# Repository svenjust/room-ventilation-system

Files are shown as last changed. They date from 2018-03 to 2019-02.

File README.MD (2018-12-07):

# Steuerung einer Lüftungsanlage für Wohnhäuser

Diese Steuerung wurde als Ersatz der Originalsteuerung entwickelt.

Das Original war Pluggit P300. Diese Steuerung funktioniert ebenso für Pluggit P450 und viele
weitere Lüftungsanlagen.

Es werden:
1. zwei Lüfter angesteuert und deren Tachosignale ausgelesen
2. vier Temperatursensoren abgefragt
3. Steuerung Abluftventilator zum Frostschutz
4. Optional: Vorheizregister als Frostschutz 
5. Optional: Sommer-Bypass geschaltet
6. Optional: Bis zu zwei Temperatur- und Feuchtigkeitssensore auslesen
7. Optional: Luftqualitätsensor (VOC) und CO2 Sensor auslesen
Die Drehzahlregelung der Lüftermotoren erfolgt durch PID-Regler. Dies sorgt dafür, das die geforderten
Drehzahlen der Lüfter sicher erreicht werden. Die Leistungssteuerung des Vorheizregisters erfolgt
ebenfalls durch einen PID-Regler.

Differenzdrucksensoren werden bisher nicht berücksichtigt.

Die Steuerung ist per LAN (W5100) erreichbar. Als Protokoll wird mqtt verwendet. Über mqtt liefert
die Steuerung Temperaturen, Drehzahlen der Lüfter, Stellung der Bypassklappe, den Status der AntiFreeze
Funktion und sonstige Werte zurück und es können verschiedene Parameter gesetzt werden.

Zusätzlich bietet die Steuerung Unterstützung für TFT Touchscreen, um einerseits die Messwerte
anzuzeigen und andererseits die Steuerung zu konfigurieren. Touchkalibrierung erfolgt bei dem
ersten Touch oder nach langen Touch auf Hauptseite (8 Sekunden). Im Verzeichnis Screenshots
befinden sich ein paar [Screenshots](Screenshots/README.md).

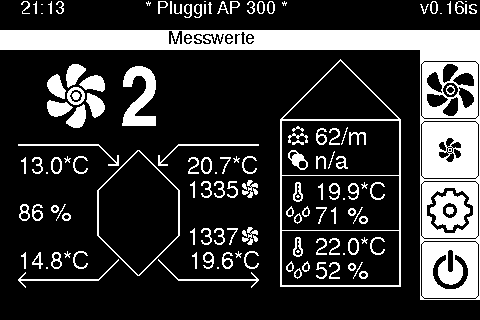
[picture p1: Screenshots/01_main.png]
Main screen


Im Verzeichnis Docs befindet sich weitere Dokumentation zu verschiedenen Themen.

Um das Projekt zu bauen müssen folgende Voraussetzungen erfüllt sein:
  - Folgende Libraries müssen installiert werden: SPI, EEPROM, PubSubClient,
    Adafruit_GFX_Library, DHT_sensor_library, PID, Adafruit_TouchScreen,
    DallasTemperature, Adafruit_Unified_Sensor, MCUFRIEND_kbv, OneWire,
    Wire, Ethernet
  - Das Projekt bringt eigene Libraries mit. Diese müssen ebenfalls installiert
    werden, am einfachsten als symbolische Links. Der Skript link_libs.sh
    linkt die Libraries an die (hoffentlich) richtige Stelle.

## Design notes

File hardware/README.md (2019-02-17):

Änderungen von HW-0.25 zu HW-0.26 - P300_Arduino_IF
 - Korrektur externer Displayanschluss zum Arduino

Änderungen von HW-0.23 zu HW-0.26 - P300_Display_IF
 - Korrektur Displayanschluss zum Display
 
Änderungen von HW-0.23 zu HW-0.25 - P300_Arduino_IF
 - Ergänzung von externen Pullup-Widerstand und Glättungskondensator am Tachosignal

Neu HW-0.25 - P300_Diff_Press
 - Entwurf einer Platine für den Aufbau von Differenzdrucksensoren
 
-----------------------------------------------------------------------------------------------------
12.01.2019 Version HW-0.24, nur P300_HiVolt, in die Platinenerstellung gegeben

Änderungen von HW-0.23 zu HW-0.24 - P300_HiVolt
 - Anschluss zu Relais per Schraubklemmen, anstatt Molex Stecker, wegen der schwierigen Beschaffung und Crimpen der Molex Verbindung
 - Alternative für 5V Spannung Meanwell IRM-05-5 mit 5W(1A) Leistung hinzugefügt, empfohlen bei Verwendung Display
 - Platine 3mm verlängert
 - Bohr in Mitte/unten hinzugefügt
 - Leiterbahnen zu den Lüftern auf 2mm verbreitert

 -----------------------------------------------------------------------------------------------------
09.01.2019 Version HW-0.23 in die Platinenerstellung gegeben

Änderungen von HW-0.22 zu HW-0.23 - P300_Arduino_IF
 - Linke Seite der Platine vergrößert auf ArduinoMega-Größe
 - Stecker für Displayanschluss ergänzt
 - Fünf weitere Bohrungen für Befestigung ergänzt
 - Leiterbahnen im größeren Abstand zu Durchbohrungen und Bauteilen verlegt
 - Connector für J12 I2C nach links verschoben, damit ausreichend Platz für JTS Stecker
 - Auf dem Stecker J4 sind die beiden Lüfteranschlüsse Lüfter 1 und Lüfter 2 getauscht. Damit ist der Stecker kompatibel zu Pluggit. Der Pluggit-Lüfter-Steuerstecker kann direkt aufgesteckt werden, wenn Molex Stiftleiste - KK - 1x8-polig - Stecker, Molex-Best-Nr. 22272081 verwendet wird.
 - Auf dem Stecker J4 (Lüfteranschluss) die vergessenen Masseverbindungen Pin 4 und Pin 8 ergänzt.

Änderungen von HW-0.22 zu HW-0.23 - P300_HiVolt
 - 230V Lüfteranschluss kompatibel zu Pluggit, Molex Stiftleiste - Mini-Fit Jr - 2x4-polig - Stecker, Molex-Best-Nr. 39281083
 - Stecker J3, J4 für Relais auf Molex Stiftleiste - Mini-Fit Jr - 2x3-polig - Stecker, Molex-Best-Nr. 39288060 geändert.
 - Änderung der Belegung der Stecker J3, J4 für die Verwendung es Relaisboards mit den Ralaisanschlüssen: Mitte = Stromzuführung, links = Nicht geschaltet, rechts geschaltet
 - Räumliche Trennung von 230V und Niedervoltspannungen auf der Platine
 - Bohrungen Pins Varistor auf 1mm vergrößert
 
Neu HW-0.23 - P300_Display_IF
 - Platine zum Aufstecken des Displays für die räumlich getrennte Montage von Display zu P300_Arduino_IF
 - Bohrlöcher für Befestigung hinzugefügt

Änderungen von HW-0.20 zu HW-0.21 - P300_Arduino_IF
 - Pins für Relais auf die ursprünglichen Pins zurückgelegt:
   D40 = BP_DIR, D41 = BP_POW, D42 = L2, D43 = L1
 - Pins für PWM-Signal Lüfter auf ursprüngliche Belegung zurückgelegt
   D44 = PWM_L1, D46 = PWM_L2

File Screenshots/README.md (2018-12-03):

Here a few screenshots from the controller UI:

Boot messages:

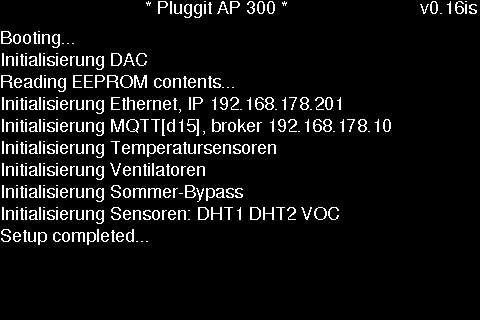
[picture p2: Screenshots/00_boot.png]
Boot


Main screen:

Main Screen
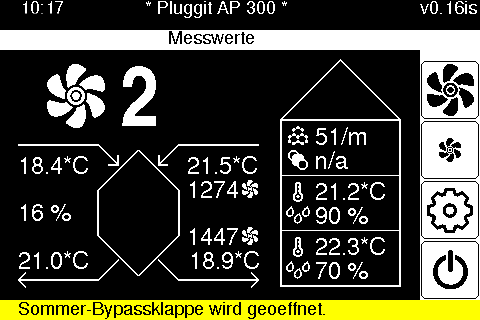
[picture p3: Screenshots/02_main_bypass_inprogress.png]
Opening Bypass

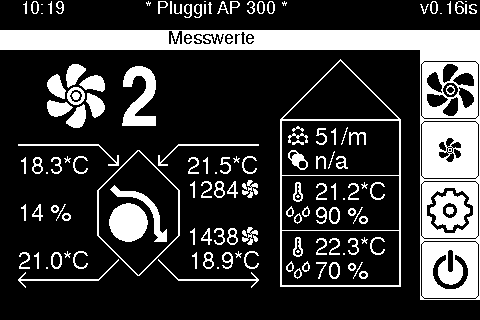
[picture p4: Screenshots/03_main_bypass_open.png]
Bypass Open

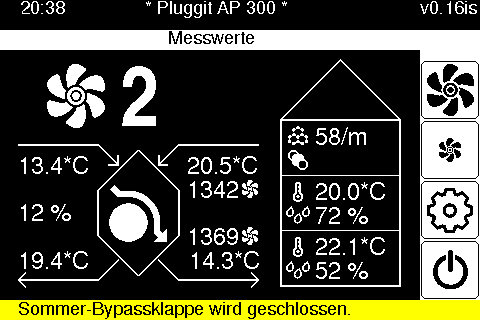
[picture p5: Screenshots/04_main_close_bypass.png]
Bypass Closing

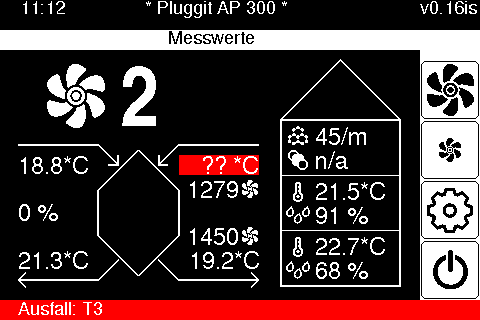
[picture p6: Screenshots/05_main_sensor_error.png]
Sensor Error


Calibration screen:

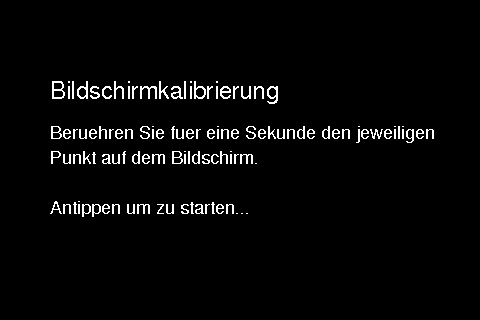
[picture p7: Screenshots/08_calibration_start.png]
Touchscreen Calibration

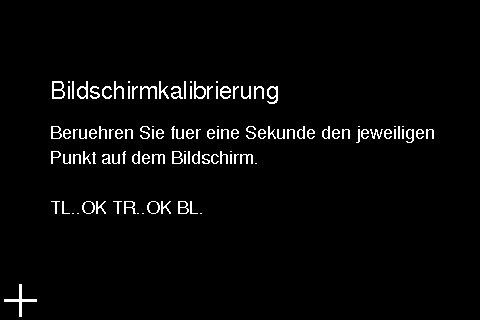
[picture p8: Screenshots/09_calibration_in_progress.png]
Touchscreen Calibration


Setup screen:

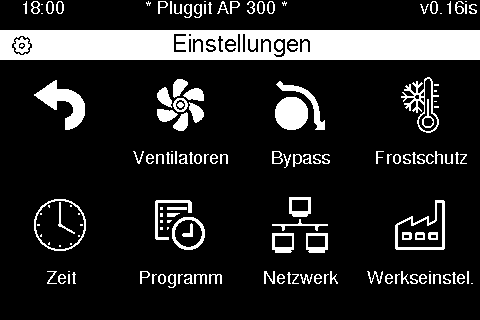
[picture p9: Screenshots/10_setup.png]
Setup


Fan setup screen:

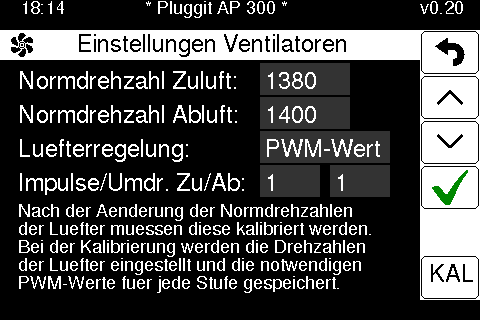
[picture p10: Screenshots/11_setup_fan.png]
Fan

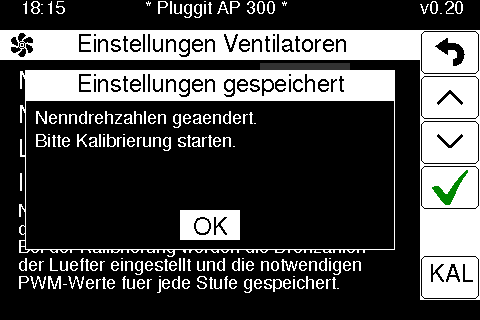
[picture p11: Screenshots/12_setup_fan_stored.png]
Fan Store

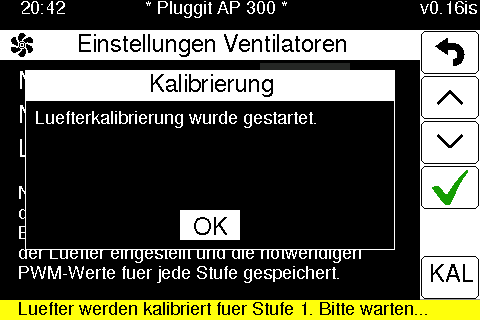
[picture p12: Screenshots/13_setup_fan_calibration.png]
Fan Calibration


Summer bypass setup screen:

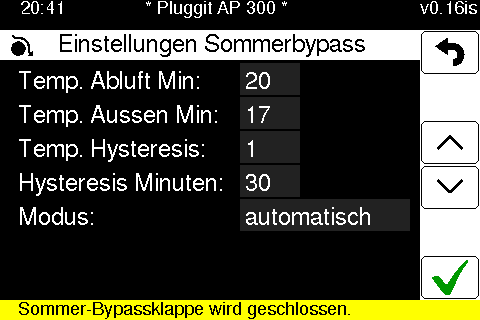
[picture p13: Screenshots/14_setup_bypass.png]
Bypass


Antifreeze setup screen:

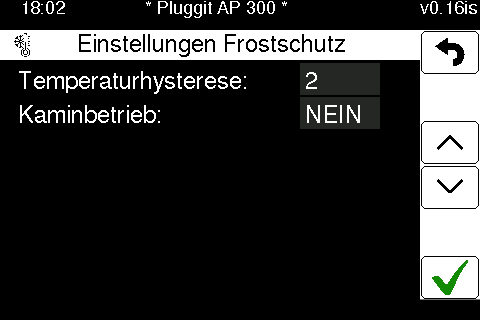
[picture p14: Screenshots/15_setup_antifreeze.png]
Antifreeze


Timezone and DST setup screen:

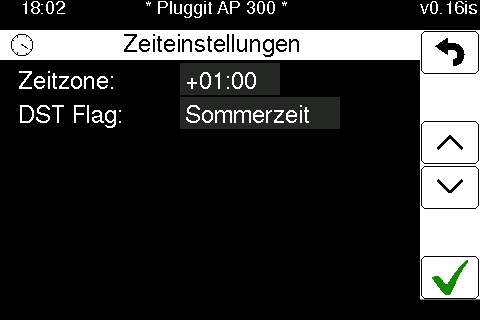
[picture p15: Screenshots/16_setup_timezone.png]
Time


Program manager screen:

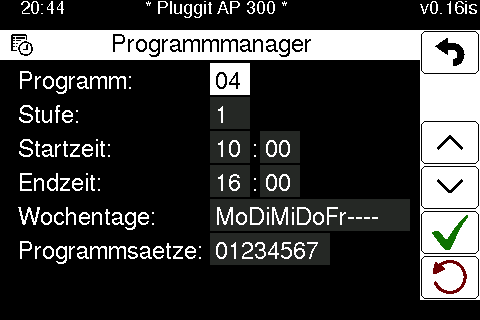
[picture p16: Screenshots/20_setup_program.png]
Program Manager

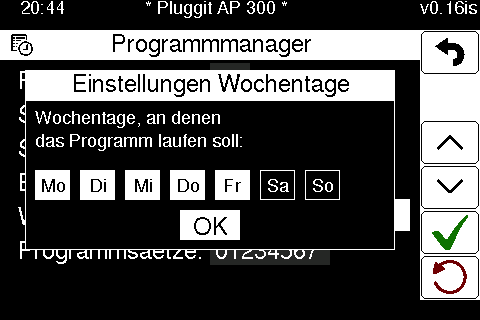
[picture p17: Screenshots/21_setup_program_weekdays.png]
Program Weekdays

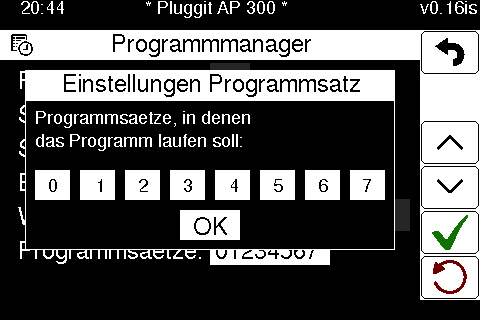
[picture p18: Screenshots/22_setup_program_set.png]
Program Sets


Network settings screen:

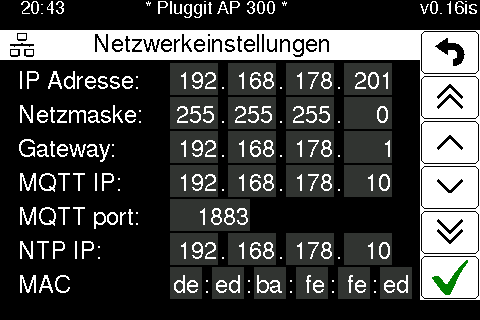
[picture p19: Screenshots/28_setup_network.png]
Network


Factory defaults screen:

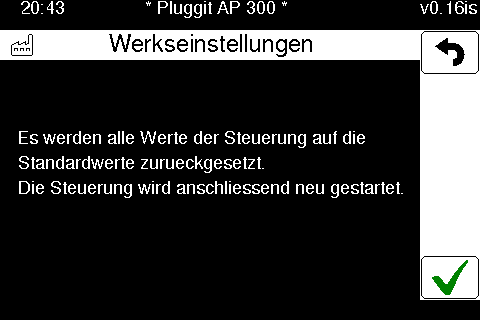
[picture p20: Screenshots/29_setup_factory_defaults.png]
Factory defaults


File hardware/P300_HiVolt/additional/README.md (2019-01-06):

# kicad
My KiCad libraries

HLK-PM02
HLK-PM03
HLK-PM12

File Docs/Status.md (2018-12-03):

# System Status Communication

The controller communicates system status via MQTT messages to a MQTT broker.
For this to work, at least the IP address and MQTT broker address have to be
configured in UserConfig.hpp (see KWLConfig::NetworkIPAddress and
KWLConfig::NetworkMQTTBroker). Network gateway address as well as DNS and NTP
server are derived from IP address by replacing the last octet with 1.

## Status MQTT Topics

Following status topics are defined:

Topic                                          | Value (Unit)      | Description
---------------------------------------------- | ----------------- | -------------------------------------------
`d15/state/kwl/heartbeat`                      | `online` / `offline` / HH:MM:SS | Online status of the system (see below).
`d15/state/kwl/statusbits`                     | `0xEEEEIIVV`      | Status bits indicating overall system state (see below).
`d15/state/kwl/fan1/speed`                     | #### (rpm)        | Speed of FAN1 (intake).
`d15/state/kwl/fan2/speed`                     | #### (rpm)        | Speed of FAN2 (exhaust).
`d15/state/kwl/aussenluft/temperatur`          | ###.## (ºC)       | Temperature of outside air.
`d15/state/kwl/zuluft/temperatur`              | ###.## (ºC)       | Temperature of inlet air.
`d15/state/kwl/abluft/temperatur`              | ###.## (ºC)       | Temperature of outlet air.
`d15/state/kwl/fortluft/temperatur`            | ###.## (ºC)       | Temperature of exhaust air.
`d15/state/kwl/effiencyKwl`                    | ## (%)            | Current efficiency.
`d15/state/kwl/lueftungsstufe`                 | typically 0-3     | Current ventilation mode.
`d15/state/kwl/dht1/temperatur`                | ###.## (ºC)       | Temperature reported by additional DHT1 sensor (if any).
`d15/state/kwl/dht2/temperatur`                | ### (%)           | Humidity reported by additional DHT1 sensor (if any).
`d15/state/kwl/dht1/humidity`                  | ###.## (ºC)       | Temperature reported by additional DHT2 sensor (if any).
`d15/state/kwl/dht2/humidity`                  | ### (%)           | Humidity reported by additional DHT2 sensor (if any).
`d15/state/kwl/abluft/co2`                     | #### (ppm)        | CO2 concentration measured by additional CO2 sensor (if any).
`d15/state/kwl/abluft/voc`                     | #### (ppm)        | Air pollutants concentration measured by additional VOC sensor (if any).
`d15/state/kwl/antifreeze`                     | `on` / `off`      | State of antifreeze protection.
`d15/state/kwl/summerbypass/flap`              | `open` / `closed` / `unknown` | State of summer bypass flap.
`d15/state/kwl/summerbypass/mode`              | `auto` / `manual` | Summer bypass mode.
`d15/state/kwl/summerbypass/TempAbluftMin`     | ### (ºC)          | Minimum outlet air temperature to consider for opening bypass flap.
`d15/state/kwl/summerbypass/TempAussenluftMin` | ### (ºC)          | Minimum outside air temperature to consider for opening bypass flap.
`d15/state/kwl/summerbypass/HystereseMinutes`  | ### (min)         | Hysteresis for bypass flap change in automatic mode.
`d15/state/kwl/summerbypass/HysteresisTemp`    | ## (ºC)           | Hysteresis temperature to open/close bypass flap.
`d15/state/kwl/heatingapp/combinedUse`         | `YES` / `NO`      | Indicates whether the ventilation system is used in conjuction with a fireplace.
`d15/state/kwl/program/index`                  | ##                | Currently running program index or -1 if none (see ProgramManager.md).
`d15/state/kwl/program/set`                    | #                 | Current program set (0-7, see ProgramManager.md).
`d15/state/kwl/program/`                       | (program string)  | Returned in response to program query (see ProgramManager.md).

NOTE: MQTT topics will be changed in the future to harmonize the language used
(with legacy topic compatibility).

## Heartbeat

The controller sends a heartbeat message once every 30s (by default, it can be configured
or turned off using KWLConfig::HeartbeatPeriod). This message either contains the word
`online` or time in format HH:MM:SS (if NTP is available and KWLConfig::HeartbeatTimestamp
is set to true).

If the connection to the broker breaks, a will message with value `offline` will
be left at the broker, so attached clients can react to the event.

## Status Bits

Status bits in form of a hexadecimal number `0xEEEEIIVV` indicate the overall status
of the system. Top 4 digits indicate error conditions, mid 2 digits indicate additional
information and lower 2 digits contain additional information value.

Error condition flags are OR-ed together to form an error status (`EEEE`):
    * 0001 - FAN1 (intake) not working
    * 0002 - FAN2 (exhaust) not working
    * 0004 - crash presence bit (see Programming/CrashDebugging.md)
    * 0008 - NTP time not yet synchronized or NTP server not answering
    * 0010 - T1 sensor (outside air) not working
    * 0020 - T2 sensor (inlet air) not working
    * 0040 - T3 sensor (outlet air) not working
    * 0080 - T4 sensor (exhaust air) not working

Info messages contain info type (`II`) and info value (`VV`). Following info types
are currently defined:
    * 00 - no additional information
    * 01 - calibration in progress, value indicates which mode is being calibrated
    * 02 - antifreeze is trying to raise temperature using preheater, value indicates
           preheater strength in %
    * 03 - antifreeze turned off one or both fans, value indicates 0 only intake,
           1 also exhaust, for fireplace mode
    * 04 - summer bypass is opening (value 1) or closing (value 0)

## Sensor Values

Sensor values for FAN1, FAN2 and temperature sensors are self-explanatory.

Sensor values for DHT1, DHT2, CO2 and VOC sensors will be only communicated, if
respective sensors are actually installed.

## Ventilation Mode

Current ventilation mode will be communicated upon change and periodically.

## Summer Bypass

Summer bypass state values are communicated when the state of the bypass changes and
periodically.

Summer bypass configuration is only communicated on-demand.

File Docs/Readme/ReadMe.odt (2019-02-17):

Ersatzsteuerung für eine Lüftungsanlage für Wohnhäuser
mit Touch-Display und
mqtt Anbindung


Abbildungsverzeichnis

Abbildung 1: Schaltplan Interface Sensoren – Arduino 10

Abbildung 2: Bestückte Interface Platine Sensoren Arduino mit Molexsteckverbindungen 11

Abbildung 3: HiVolt Schaltplan mit Schaltnetzteil(en) und Pluggit Lüfteranschluss 11

Abbildung 4: Bestückte HiVolt Platine 12

Abbildung 5: Schaltplan Display Platine 14

Abbildung 6: Display Platine zum Aufstecken des Displays 14

Abbildung 7: Kalibrieren des Touchdisplay 20

Abbildung 8: Kalibrierung Touch wird gestartet 20

Abbildung 9: Fehlerhafte Erkennung des Tachosignals (rpm) 23

Abbildung 10: Korrekte Erkennung des Tachosignals (rpm) 24

Abbildung 11: Arduino Mega 2560 REV Bild von Dsimic - Eigenes Werk, CC BY-SA 4.0, https://commons.wikimedia.org/w/index.php?curid=35850081 31

# Sicherheitshinweis

ACHTUNG 230V, LEBENSGEFAHR

EIGENES RISIKO BEIM NACHBAU

Die Lüfter, der Bypass und das Vorheizregister werden mit 230V Versorgungsspannung betrieben bzw. mit 230V Spannung (Bypass) gesteuert.

Für den Betrieb der Lüftungsanlage mit einer Feuerstätte ohne Fremdluftzufuhr, siehe Abschnitt 6.2

# Einführung

## Ziel

Ziel dieser Entwicklung ist es, defekte Steuerungen von Lüftungsanlagen für Wohnhäuser durch diese Eigenentwicklung zu ersetzen. Die Entwicklung des Projekt erfolgt in Freizeit als Hobby. Für die Entwicklung werden Standardbauteile verwendet. Dies sind: Arduino Mega, ein LAN-Modul, OneWire Temperatursensoren DS18B20, optional ist die Ansteuerung eines Vorheizregisters, die Ansteuerung für den Sommer-Bypass, Sensoren für CO2, VOC und Luftfeuchtigkeit sowie ein (Touch-) Grafikdisplay für die lokale Anzeige. Die Lüfter können per Optokoppler oder separaten DAC Digital Analog Converter (0-10V) angeschlossen werden. Diese Steuerung implementiert eine MQTT Schnittstelle für die Verbindung zur Haussteuerung.

Die Steuerung wurde ursprünglich für eine Pluggit P300 Anlage entwickelt, funktioniert ebenso für Pluggit P450 und viele weitere Lüftungsanlagen. Die elektrische Anpassung für unterschiedliche Lüftungsanlagen wird im Abschnitt Hardware beschrieben.

Die Steuerung implementiert die wesentlichen Funktionen zum technisch sicheren Betrieb der Lüftungsanlage. Die Frostschutzabschaltung des Zuluftventilators ist immer aktiv, eine Vereisung und damit ggfs Zerstörung des Wärmetauschers sollte damit ausgeschlossen sein. Voraussetzung ist der korrekte Anschluss der Temperatursensoren. Die Autoren dieser Software übernehmen KEINERLEI Garantie. Es werden die folgenden Sensoren/Aktoren geschaltet.

- zwei Lüfter werden angesteuert und deren Tachosignale werden ausgelesen
- vier Temperatursensoren werden abgefragt
- Steuerung des Zuluftventilator zum Frostschutz
- Steuerung des Abluft- und des Zuluftventilators zum Frostschutz bei Kaminbetrieb
- Optional: Vorheizregister als Frostschutz
- Optional: Sommer-Bypass geschaltet
- Optional: Bis zu 2 Temperatur/Luftfeuchtesensoren (DHT22)
- Optional: CO2-Sensor MH-Z14
- Optional: VOC-Sensor

Diese Steuerung stellt eine MQTT Schnittstelle zur Verfügung und kann darüber mit Automatisierungssystemen kommunizieren. Alle Topics der MQTT Schnittstelle sind in https://github.com/svenjust/room-ventilation-system/tree/master/Docs/mqtt%20topics dokumentiert.

Komfortfunktionen, wie die Regelung der Lüftungsanlage anhand eines VOC Sensors, sind nicht implementiert. Diese Regelungsaufgaben können in übergeordneten Haussteuerung besser, weil spezifischer für den eigenen Anwendungsfall, implementiert werden. Der Autor verwendet fhem für diese Aufgaben. Die Einbindung dieser Steuerung in fhem wird im Abschnitt 9 beschrieben. Die Messwerte der evtl. verbauten CO2, VOC, oder Feinstaubsensoren in der Lüftungsanlage werden per MQTT gepublishet.

## Systemaufbau

Die Steuerung der Lüftungsanlage kann autark betrieben werden.

Sinnvoll ist ein Betrieb mit einer übergeordneten Haussteuerung. Die Installation von fhem und eines MQTT Brokers werden vorausgesetzt und sind nicht Inhalt dieses Papiers.

## Regelungsstrategie der Steuerung

Der Inbetriebnehmer muss die Normdrehzahl für Zu- und Abluftventilator vorgeben. Differenzdrucksensoren sind nicht verbaut. Hersteller wie Helios verbauen auch keine solchen Sensoren. Pluggit stellt als Normdrehzahl jeweils 1.550 U/min werksseitig ein.

Die Steuerung versucht die vorgegebenen Drehzahlen für Zu- und Abluftventilator zu erreichen. Dem Lüfter wird als Stellgröße ein PWM-Signal oder eine Gleichspannung 0-10V vorgegeben. Über die Tacholeitung teilt der Lüfter über ein PWM Signal seine aktuelle Drehzahl mit. Im Normalbetrieb der Steuerung findet keine Regelung der Drehzahl statt. Die Steuerung kann in den Kalibrierungbetrieb gesetzt werden. Die Lüfter fahren dann die, für die verschiedenen Lüftungsstufen notwendigen Drehzahlen an, und ermitteln per PID-Regler das jeweils notwendige PWM-Signal. Das PWM-Signal für die Drehzahl für jede Lüftungsstufe wird dann getrennt für jeden Lüfter im EEPROM gespeichert. Im Normalbetrieb wird der Lüfter mit dem kalibrierten PWM Signal angesteuert. Die Strategie ist ähnlich dem Betrieb des Originalhersteller, hier findet zu definierten Zeiten (Montagsmorgens) eine „Kalibrierung“ statt. Die Kalibrierung muss per Touch-Display oder per MQTT gestartet werden.

## Speicherung des Anlagenparameter

Die für einen sicheren Betrieb erforderlichen Anlagenparameter werden im EEPROM des Arduino Mega gespeichert. Der Inhalt des EEPROMs kann im Sourcecode und per MQTT-Befehl gelöscht werden. Die Anlage wird damit auf die sogenannte „Werkseinstellungen“ zurückgesetzt. Die Werkseinstellungen definieren für die P300 einen sicheren Betriebszustand.

# Hardware

Der Hardwareaufbau kann in unterschiedlichen Ausbaustufen erfolgen, ebenso können verschiedene Sensoren ergänzt werden. Zuerst wird die absolut notwendige Hardware besprochen. Weiter unten folgen optionale Teile.

## Hardwareauswahl

### Notwendige Hardware

Für die Steuerung ist ein Arduino Mega erforderlich. Für die externe Kommunikation ist ein LAN-Shield erforderlich, aufgebaut und getestet ist das System mit WizNET (W5100) Ethernet Shield, siehe 11.2.

Die Temperaturen werden mit vier Temperatursensoren DS18B20 (siehe 11.5) im Edelstahlgehäuse erfasst und einzeln mit der Steuerung verkabelt. Durch die getrennte Verkabelung können die Sensoren sicher den Luftströmen zugeordnet werden. Für jeden Temperatursensor ist ein 4,7k Widerstand erforderlich.

In den KWL Geräten sind häufig Lüfter mit 230V Anschluss und Steuerung per 10V-PWM-Signal oder per Gleichspannung 0-10V verbaut. Den genauen Lüftertyp muss jeder für seine Anlage bestimmen. In den Pluggit Geräten P300/450 sind Lüfter von Papst verbaut, ähnlich wie http://img.ebmpapst.com/products/manuals/R3G190RC0503-BA-GER.pdf verbaut. In der gerade erwähnten Anleitung, Seite 9 sind die Schaltungsmöglichkeiten des Lüfters aufgeführt. Eine einfache Ansteuerung kann bei dem vorliegenden Lüfter durch Optokoppler erfolgen. Die Optokoppler werden direkt mit dem Lüfter verbunden, siehe Bild 1. Das Tachosignal kann direkt mit dem Arduino verbunden werden.

Hardwareliste (Mindestausstattung):

- 1 x Arduino Mega 2560
- 1 x LAN Module WizNET (W5100) Ethernet Shield
- 4 x OneWire DS18B20 in Edelstahlhülse

Die vollständige Bauteillisten sind im Abschnitt 10 aufgeführt.

#### Platine für Verbindung der Sensoren und Lüfter mit dem Arduino

Für die Verbindung des Arduino Mega mit den Lüftern, Temperatursensoren, Relaisboard und weiteren Sensoren ist in diesem Projekt ein Interface Board entwickelt worden. Der Stecker für die Lüftersteuerung kann direkt von der Pluggitplatine umgesteckt werden

Die technischen Unterlagen zu den Boards und die Gerberfiles für die Erstellung sind bei Github verfügbar https://github.com/svenjust/room-ventilation-system/tree/master/hardware.

#### Spannungsversorgung

Für die Spannungsversorgung gibt es zwei Alternativen. Zum einen ist eine Platine zum Anschluss der 230 V-Lüfter und Netzteil verfügbar. Zum anderen kann ein Standardnetzteil verwendet werden.

Auf der unten vorgestellten Platine für Spannungsversorgung können neben integrierten Step-Down-Netzteilen für 5V und 12V auch die 230V Stecker der Lüfter direkt von der Pluggitplatine umgesteckt werden. Die Platine enthält ist mit einer Littelfuse-Sicherung und einem Varistor als Überspannungsschutz aufgebaut.

### Alternative und optionale Hardware

#### Alternativ: DAC 0-10V für Vorheizregister und Lüfter

Alternativ zu den Optokopplern können die Lüfter mit einem 0-10V Gleichstromsignal angesteuert werden. Ein Arduino kann eine solche Gleichspannung nicht direkt zur Verfügung stellen. Ein Digital-Analog-Converter (DAC) wie z.B. https://www.horter-shop.de/de/home/93-bausatz-i2c-analog- (https://www.horter-shop.de/de/home/93-bausatz-i2c-analog-input-modul-5-kanal-10-bit-4260404260752.html)input-modul-5-kanal-10-bit-4260404260752.html (https://www.horter-shop.de/de/home/93-bausatz-i2c-analog-input-modul-5-kanal-10-bit-4260404260752.html) stellt die erforderliche Spannung bereit und kann einfach vom Arduino angesteuert werden.

Wenn ein Vorheizregister verwendet werden soll, ist die Ansteuerung per DAC evtl. notwendig.

#### Optional: TouchDisplay

Für eine Visualisierung am Gerät bzw. eine Bedienung ohne Automatisierungssystem kann ein Touchdisplay (siehe 11.6) verwendet werden. Die Steuerung setzt auf die mcufriend-Library auf und geht von einer Auflösung von 480x320 Pixel aus. Das Touchdisplay sollte wenigstens 3,5“ groß sein.

#### Optional: Platine für abgesetztes TouchDisplay

Das Display kann entweder direkt auf dem LAN Shield oder per Kabelverbindung entfernt von der Steuerung vor oder auf der Lüftungsanlage betrieben werden. Die direkte Verbindung mit dem LAN Shield kann beim Testen interessant sein. Für die entfernte Anbindung ist eine Platine verfügbar.

#### Optional: Sommer-Bypass per Relais

Wenn das Gerät einen Sommer-Bypass eingebaut hat, kann dieser ansteuert werden. Die Steuerung enthält die dafür notwendigen Funktionen.

GEFAHR: Verschiedene Gerätehersteller bauen bzgl der Ansteuerspannung unterschiedliche Lösungen ein. Hier ist vor Beginn genau zu prüfen, was im eigenen Gerät verbaut.

In Pluggit-Geräten der Serien P300/450 wird der Sommer-Bypass mit 230V~ geschaltet. Die Schaltung entspricht der klassischen Rolladensteuerung, d.h. für die Fahrdauer wird eine Spannung angelegt und nach Ausschalten der Spannung bleibt der Bypass in der aktuellen Stellung stehen.

Helios schaltet den Sommer-Bypass mit 24V=.

Die Schaltung für den Sommer-Bypass entspricht klassischen Rolladensteuerung, es werden zwei Relais verbaut, das erste Relais schaltet die Spannung, das zweite (Wechsel-) Relais bestimmt die Fahrrichtung.

#### Optional: CO2 Sensor

Mit dem folgenden CO2 Sensor hat der Autor gute Erfahrungen gemacht: MH-Z14, https://www.sensor-test.de//ausstellerbereich/upload/mnpdf/en/MHZ14_14.pdf . Das Signal wird über eine serielle Schnittstelle übertragen.

Die Messwerte des CO2 Sensors werden per MQTT an übergeordnete Geräte übertragen. Eine Regelung der Lüftungsanlage anhand des CO2-Sensors, ist nicht implementiert. Diese Regelungsaufgaben kann in einer übergeordneten Haussteuerung besser, weil spezifischer für den eigenen Anwendungsfall, implementiert werden.

Der CO2 Sensor kann im Abluftstrom der Lüftungsanlage verbaut werden.

#### Optional: VOC Sensor

Der Autor verwendet den folgenden VOC Sensor Figaro TGS2600, http://www.figarosensor.com/products/2600pdf.pdf . Das Signal wird durch einen Widerstandswert übertragen. Für das Steuern der Lüftungsanlage ist der VOC Sensor nach Erfahrung des Autors ausreichend, der CO2-Sensor dient eher dem Spiel- und Messtrieb. Beide Werte korrelieren weitgehend.

Die Messwerte des VOC Sensors werden per MQTT an übergeordnete Geräte übertragen. Eine Regelung der Lüftungsanlage anhand des VOC-Sensors, ist nicht implementiert. Diese Regelungsaufgaben kann in einer übergeordneten Haussteuerung besser, weil spezifischer für den eigenen Anwendungsfall, implementiert werden.

Der VOC Sensor kann im Abluftstrom der Lüftungsanlage verbaut werden.

#### Optional: Luftfeuchtesensoren DHT22

Für die Messung der Luftfeuchte im Abluft- und Zuluftstrom können bis zu zwei DHT22 Sensoren eingebaut werden. Die Messwerte der Sensoren werden per MQTT an übergeordnete Geräte übertragen. Eine Regelung der Lüftungsanlage anhand der DHT22-Sensoren, ist nicht implementiert.

## Schaltpläne

### Interface Platine für Anschluss der Sensoren

Abbildung 1: Schaltplan Interface Sensoren – Arduino

Für die Verbindung zu den Lüftern wird ein achtpoliger Molex-Stecker mit der Bezeichnung:Molex_KK-254_AE-6410-08A_1x08_P2.54mm_Vertical empfohlen. Damit kann der Stecker der Pluggit-Platine direkt umgesteckt werden, das Pinlayout ist identisch.

Für die anderen 2-, 3-, 4-, 6- und 8-poligen Steckverbindern können Stecker mit 2,54mm Pinabstand verwendet werden. Dies können Steckverbinder aus der Molex-KK-254-Reihe oder auch JST XH-Reihe sein. Die JST XH-Reihe ist aktuell leichter und zu geringeren Kosten verfügbar.

Abbildung 2: Bestückte Interface Platine Sensoren Arduino mit Molexsteckverbindungen

### HiVolt Platine für Stromversorgung und 230V Anschluss der Lüfter

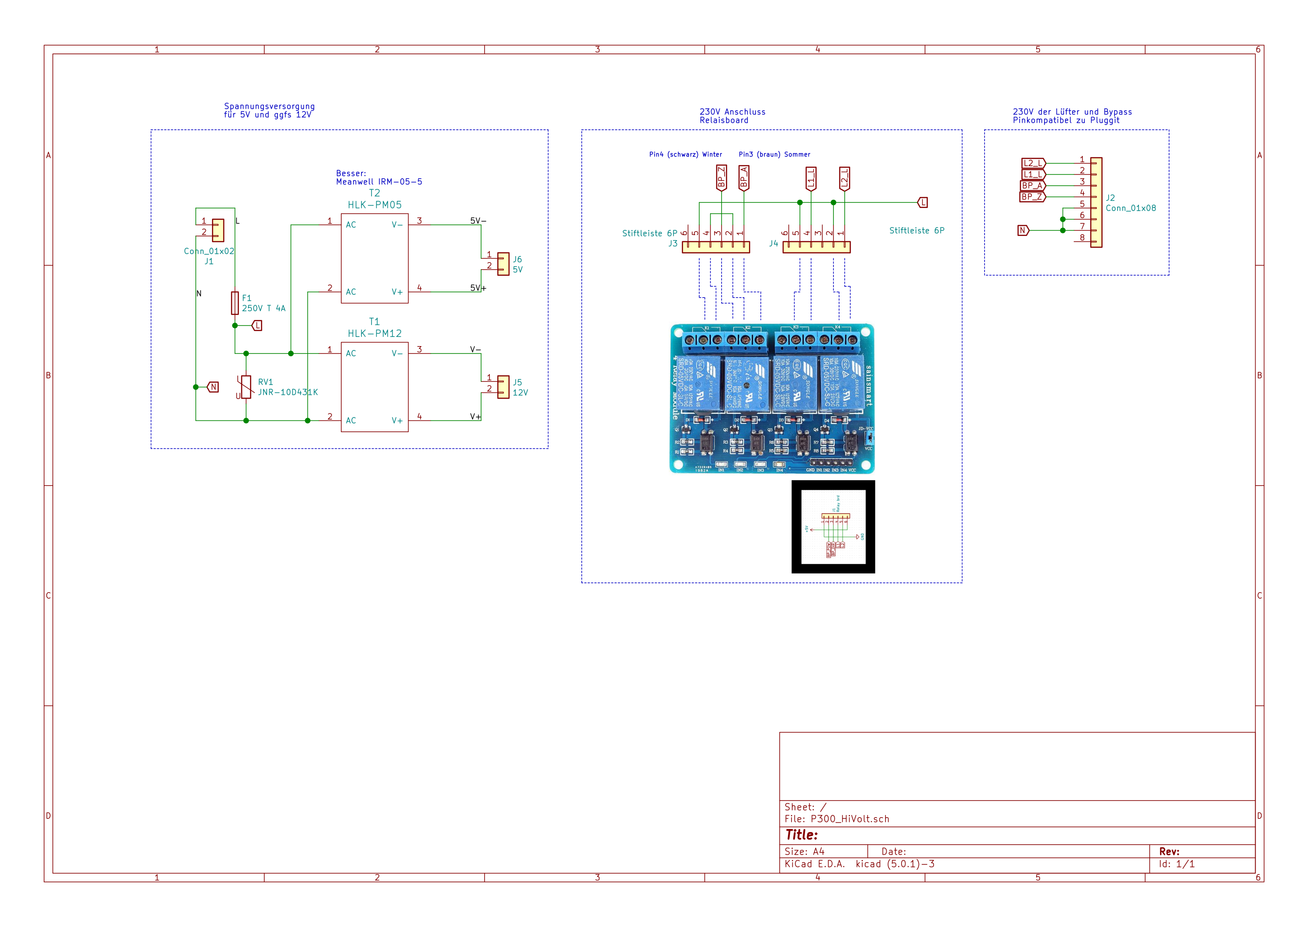
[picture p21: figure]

Abbildung 3: HiVolt Schaltplan mit Schaltnetzteil(en) und Pluggit Lüfteranschluss

Für das 5V Schaltnetzteil wird ein Meanwell IRM-05-5 empfohlen, dieses leistet bis zu 1A. Das HLK-PM5 kann beim Betrieb ohne Display verwendet werden. Die 12V Spannungsversorgung ist optional.

Für die 230V Verbindung zu den Lüftern wird der Connector Molex_Mini-Fit_Jr_5566-08A_2x04_P4.20mm_Vertical verwendet, dieser ist pinkompatible zu den Pluggit-Steckern, der Stecker kann umgesteckt werden.

Für den 230V Eingangsstecker wird Molex_Mini-Fit_Jr_5566-02A_2x01_P4.20mm_Vertical empfohlen, wiederum pinkompatible zu Pluggit.

Abbildung 4: Bestückte HiVolt Platine

### Interface Platine für Display

Abbildung 5: Schaltplan Display Platine

Abbildung 6: Display Platine zum Aufstecken des Displays

Die Interface Platine zum Display ermöglicht lediglich die einfache Befestigung und Verwendung von Steckern zwischen Display und Controller. Die Platine enthält keine weiteren Bauelemente.

## Aufbau der Platinen

Es wird ein fachkundigen Aufbau der Schaltung vorausgesetzt. Dabei ist zwischen der Niederspannungsseite und der 230V-Seite zu trennen.

Für den Aufbau der Schaltung existieren fertige Platinen. Die Verbindungen der Bauteile sind zu löten, bzw. zu schrauben. Nach dem Löten sind die Lötverbindungen zu kontrollieren.

Der Arduino Mega, die Interface Platine und das LAN Shield werden in der Reihenfolge von unten nach oben aufeinander gesteckt. Bei einer Verschraubung der Platinen sind Kunststoffschrauben zu verwenden.

Für die Befestigung der Platinen in der Lüftungsanlage kann als Träger eine zugeschnittene PVC Platte (Bastelplatte) verwendet werden. Um die Festigkeit zu erhöhen können links und rechts schmale Verstärkungen hochkant aufgeklebt werden. Die PVC Platte sorgt gleichzeitig für eine elektrische Trennung, insbesondere der HiVolt-Platine, gegenüber dem Gehäuse der Lüftungsanlage. Bei vollständiger Bestückung der HiVolt-Platine können die 230V führenden Leiterbahnen damit nicht mehr direkt berührt werden.

### Bestückung der Interface Platine

Die Bestückung der Interface Platine sollte mit den Optokopplern starten. Anschließend die Stecker der Kabelverbinder und die Verbinder zum Arduino einlöten. Für die korrekte Ausrichtung der Verbinder zum Arduino ist es sinnvoll, die Stiftleisten in den Arduino Mega zu stecken und anschließend erst die Platine auf die Stiftleisten zu stecken. Die Stiftleisten dann auf der Platine verlöten. Für die Stiftleisten zum LAN-Modul den Platine vom Arduino entfernen und die Stiftleisten mit dem LAN-Modul verbinden, die Platine auflegen und von unten verlöten. Nachfolgend die stehenden Widerstände und ggf. Kondensatoren einlöten.

Zu Abschluss der Bestückung auf Fehler (Lötbrücken, kalte Lötstelle) kontrollieren.

### Bestückung der HiVolt Platine

Die Bestückung der HiVolt Platine sollte mit der Fassung für die Sicherung und dem Varistor starten. Nachfolgend die Verbinder und Schaltnetzteile einlöten.

Zu Abschluss der Bestückung auf Fehler (Lötbrücken, kalte Lötstelle) kontrollieren.

### Bestückung der Interface Platine zum Display

Auf der Interface Platine müssen die Stiftleisten zum Display verlötet werden. Der Anschluss der Leitungen zur Interface Platine zum Arduino kann abhängig von der gewünschten Bauhöhe unterschiedlich ausgeführt werden, hier ist lediglich auf die korrekte Polung zu achten, Pin 1 ist bei beiden Verbindern gekennzeichnet.

Zu Abschluss der Bestückung auf Fehler (Lötbrücken, kalte Lötstelle) kontrollieren.

# Grundeinstellungen Soucecode

Die benutzerdefinierten Einstellungen sollen in der Datei UserConfig.h erfolgen. Diese Einstellungen bleiben auch bei einem Update des Sourcecodes erhalten. Die Syntax in der UserConfig.h lautet:

CONFIGURE(name, value)
CONFIGURE(name, values…)

Weitere Hinweise siehe in der Datei KWLConfig.h

## Definition der Anschlüsse

Abhängig vom tatsächlichen Aufbau der Hardware müssen die Anschlüsse (PINs) für Ein- und Ausgänge kontrolliert bzw. umdefiniert werden, insbesondere werden Displays unterschiedlich angeschlossen. Aktuell verwenden wir Displays für die Anschlüsse A0-A9 und 0-13.

Für die Auswertung des Tachosignals der Lüfter sind Interrupt-fähige Eingänge notwendig, aktuell Pin 18, 19. Das PWM Signal für die Lüfter wird an Pin 44 und Pin 46 bereitgestellt.

Der DAC verwendet die Anschlüsse 20 und 21.

Der CO2-Sensor MH-Z14 verwendet die zweite seriellen Schnittstelle Serial2, Pin 16 und 17.

Die Temperatursensoren DS18B20 verwendet die Pins 30 bis 33.

Die Luftfeuchtesensoren DHT1 und DHT2 verwenden die Pins 28 und 29.

Das Relais für den Bypass und die Lüfter verwendet die Anschlüsse 40 bis 43.

Der VOC Sensor verwendet den Analogeingang A15.

Im Sourcecode beginnt und endet der konfigurierbare Bereich mit „A N S C H L U S S E I N S T E L L U N G E N“

## Netzwerkeinstellungen

Es muss die MAC- und die IP Adresse, Subnet, Gateway, DNS dieser Steuerung einstellt werden, ebenso die IP-Adresse des mqtt-Brokers.

CONFIGURE(NetworkIPAddress, 192, 168, 20, 201)
CONFIGURE(NetworkGateway, 192, 168, 20, 250)
CONFIGURE(NetworkDNSServer, 192, 168, 20, 250)
CONFIGURE(NetworkNTPServer, 192, 168, 20, 250)
CONFIGURE(NetworkMACAddress, 0x02, 0xC8, 0x07, 0xC2, 0x35, 0x81 )

## Werkseinstellung

Die für einen Betrieb erforderlichen Anlagenparameter werden im EEPROM des Arduino Mega gespeichert.

Durch das Setzen von #define FACTORY_RESET_EEPROM true wird bei jedem Neustart der Steuerung der EEPROM-Speicher des Arduinos gelöscht und mit den Werkseinstellungen überschrieben. Für den regulären Betrieb muss #define FACTORY_RESET_EEPROM false definiert sein. Das EEPROM des Arduinos ist für 100.000 Schreibzyklen ausgelegt.

Alternativ kann das EEPROM mit dem

mosquitto_pub -t d15/set/kwl/resetAll_IKNOWWHATIMDOING -m YES

gelöscht werden. Anschließend wird die Steuerung neu gestartet.

Es sind die folgenden „Werkseinstellungen“ definiert. Die können in der Datei „UserConfig.h“ überschrieben werden.

Name | Wert | Beschreibung
StandardModeCnt | 4 | Anzahl der unterschiedlichen Lüftungsstufen
StandardKwlModeFactor | {0, 0.7, 1, 1.3} | Definition der Drehzahl je Stufe in Relation zu defStandardSpeedSetpointFan
StandardKwlMode | 2 | Standardlüftungsstufe beim Einschalten.
StandardSpeedSetpointFan1 | 1550 | Drehzahl in Standardlüftungsstufe für den Zuluftventilator
StandardSpeedSetpointFan2 | 1550 | Drehzahl in Standardlüftungsstufe für den Abluftventilator
StandardFan1ImpulsesPerRotation | 1.0 | Anzahl der Impulse am Tachosignal pro Umdrehung des Lüfters
StandardFan2ImpulsesPerRotation | 1.0 | Anzahl der Impulse am Tachosignal pro Umdrehung des Lüfters
StandardKwlFanPrecisionPercent | 1.5 | Max Abweichung der Istdrehzahl zur Solldrehzahl bei Kalibrierung in Prozent
StandardNenndrehzahlFan | 3200 | Nenndrehzahl des verbauten Ventilators, siehe Typenschild. Die Nenndrehzahl wird benötigt für die Berechnung der Ansteuerung im unkalibrierten Betrieb
StandardBypassTempAbluftMin | 24 | Mindestablufttemperatur für die Öffnung des Bypasses im Automatik Betrieb
StandardBypassTempAussenluftMin | 13 | Mindestaussenlufttemperatur für die Öffnung des Bypasses im Automatik Betrieb
StandardBypassHystereseMinutes | 60 | Hysteresezeit für eine Umstellung des Bypasses im Automatik Betrieb
StandardBypassHysteresisTemp | 3 | Hysteresetemperatur für eine Umstellung des Bypasses im Automatik Betrieb
StandardBypassManualSetpoint | 1 (Closed) | Stellung der Bypassklappen im manuellen Betrieb
StandardBypassMode | 0 (Auto) | Automatik oder manueller Betrieb der Bypassklappe. Im Automatikbetrieb steuert diese Steuerung die Bypass-Klappe, im manuellen Betrieb wird die Bypass-Klappe durch mqtt-Kommandos gesteuert.
StandardAntifreezeHystereseTemp | 3 | Hysteretemperatur für Steuerung von Antifreeze
StandardHeatingAppCombUse | false | Einstellung für den Feuerstättenbetrieb. false = keine Feuerstätte, true = Feuerstätte, Kamin, Ofen ohne Fremdluftzufuhr
StandardDST | false | Daylight savings time default settings.
StandardTimezoneMin | 60 | Standard time zone offset in minutes (CET, GMT+1).

## Ansteuerung der Relais

Für die Lüfter und den Sommer-Bypass können bis zu vier Relais verbaut sein. Ohne Sommer-Bypass kann die Steuerung auch ohne Relais betrieben werden. Da verschiedene Relais unterschiedlich geschaltet werden, kann hier die logische Schaltung definiert werden.

RELAY_ON | LOW | Daylight savings time default settings.
RELAY_OFF | HIGH | Standard time zone offset in minutes (CET, GMT+1).

## Debugausgaben

### Debugausgaben auf der seriellen Schnittstelle

Es können Debugausgaben auf der seriellen Schnittstelle für unterschiedliche Bereiche ein oder ausgeschaltet werden. Nach Änderung muss der Sourcecode neu kompiliert werden.

// *************************************************** D E B U G E I N S T E L L U N G E N ********************************************************

// Allgemeine Debugausgaben auf der seriellen Schnittstelle aktiviert.

static constexpr bool serialDebug = false;

// Debugausgaben für die Lüfter auf der seriellen Schnittstelle aktiviert.

static constexpr bool serialDebugFan = false;

// Debugausgaben für die Antifreezeschaltung auf der seriellen Schnittstelle aktiviert.

static constexpr bool serialDebugAntifreeze = false;

// Debugausgaben für die Summerbypassschaltung auf der seriellen Schnittstelle aktiviert.

static constexpr bool serialDebugSummerbypass = false;

// Debugausgaben für die Displayanzeige.

static constexpr bool serialDebugDisplay = false;

// Debugausgaben für die Sensoren.

static constexpr bool serialDebugSensor = false;

// Debugausgaben für das Programm.

static constexpr bool serialDebugProgram = false;

// *******************************************E N D E *** D E B U G E I N S T E L L U N G E N *****************************************************

### Debugausgaben per mqtt

Es können Debugausgabe per mqtt ein- und ausgeschaltet, sowie per mqtt übertragen werden. Dazu ist in der UserConfig.h

#define DEBUG

zu definieren. Anschließend können die Debugausgaben zur Laufzeit per mqtt ein- und ausgeschaltet werden. Die mqtt Topics sind in der Datei https://github.com/svenjust/room-ventilation-system/Docs/mqtt topics/mqtt_topics.ods beschrieben.

# Build der Software für Arduino

Die Software wird in der Arduino IDE gebaut. Debugausgaben für die serielle Schnittstelle können im Code aktiviert werden, siehe 4.5.1

## Notwendige Bibliotheken

Für das Bauen der Steuerung sind Bibliotheken notwendig.

- SPI,
- EEPROM,
- PubSubClient,
- Adafruit_GFX_Library,
- DHT_sensor_library,
- PID,
- Adafruit_TouchScreen,
- DallasTemperature,
- Adafruit_Unified_Sensor,
- MCUFRIEND_kbv,
- OneWire,
- Wire,
- Ethernet

Das Projekt bringt eigene Libraries mit. Diese müssen ebenfalls installiert werden, am einfachsten als symbolische Links. Der Skript link_libs.sh linkt die Libraries an die (hoffentlich) richtige Stelle.

Aktuelle Infos sind zu finden unter: https://github.com/svenjust/room-ventilation-system

# Inbetriebnahme

Vor der Inbetriebnahme sind unbedingt die Pinbelegungen für die Motoren und Sensoren, die Netzwerkeinstellungen und die „Werkseinstellungen“ zu kontrollieren und entsprechend den eigenen Bedürfnissen einzustellen. WICHTIG: Wenn Werkseinstellungen im Sourcecode geändert werden, muss das EEPROM gelöscht werden, damit die neuen Werkeinstellungen verwendet werden, siehe 4.3.

Eine schrittweise Inbetriebnahme wird empfohlen. Die Inbetriebnahme kann über das Touchdisplay oder den MQTT Broker erfolgen, diese Anleitung geht vom funktionierenden MQTT Broker aus.

## Displaykalibrierung

Für die Inbetriebnahme und auch für den späteren Betrieb der Anlage ist ein Display hilfreich. Der Touch vom Display muss nach dem Zusammenbau bzw. bei Änderung der Verbindung zwischen Display und Controller neu kalibriert werden. Dazu 10 Sekunden den Touch berühren, die Display-Kalibrierung wird gestartet.


Abbildung 8: Kalibrieren des Touchdisplay

Anschließend den Anweisung auf dem Display folgen.


Abbildung 9: Kalibrierung Touch wird gestartet

## Feuerstättenmodus (Kaminbetrieb)

Wenn eine Feuerstätte (Kamin/Ofen) im Haus ohne Fremdluftzufuhr betrieben wird, besteht die Gefahr, dass bei negativen Außentemperaturen der Zuluftlüfter abgeschaltet wird und giftiges Kohlenmonoxid (CO) aus der Feuerstätte in das Haus gesaugt werden.

- LEBENSGEFAHR -

Mit dem Einstellen des Feuerstättenmodus werden im Antifrostbetrieb beide Lüfter für vier Stunden ausgeschaltet. Das Wiedereinschalten vor vier Stunden ist nur durch einen Neustart der Steuerung möglich.

Der Feuerstättenmodus kann auf zwei Arten eingeschaltet werden, entweder im Sourcecode oder durch Zusenden einer MQTT Nachricht. Bei beiden Arten wird die Einstellung im EEPROM gespeichert und bleibt bei einem Neustart erhalten. Empfohlen wird die Einstellung im Sourcecode anzupassen, da diese Einstellung auch bei einer Rücksetzung auf Werkeinstellungen erhalten bleibt.

In der UserConfig muss eingestellt werden:

CONFIGURE(StandardHeatingAppCombUse, true)

Anschließend ist eine Rückstellung auf Werkseinstellungen notwendig, siehe 4.3.

Alternativ kann folgendes per MQTT an die Steuerung geschickt werden:

mosquitto_pub -t d15/set/kwl/heatingapp/combinedUse -m YES

Diese Einstellung wird gespeichert, aber bei einer Werkeinstellungen zurückgesetzt!

Beim Starten der Steuerung kann die Einstellung überprüft werden, es wird beim Feuerstättenmodus ausgegeben:

...System mit Feuerstaettenbetrieb

## Optional, aber empfohlen: MQTT Broker

Für den Betrieb ist ein MQTT Broker sinnvoll. Die Installation eines MQTT Brokers ist an vielen Stellen im Netz beschrieben, u.a. hier: https://wiki.fhem.de/wiki/MQTT_Einf%C3%Bchrung (https://wiki.fhem.de/wiki/MQTT_Einführung). Wenn der MQTT-Broker installiert ist und die Steuerung gestartet wird, so sendet die Steuerung alle 30 Sekunden ein Heartbeat Signal, diese kann bei einem Mqtt-Client mit

mosquitto_sub -v -h localhost -t d15/state/kwl/heartbeat

abonniert werden.

## Temperatursensoren

Die vier Temperatursensoren (DS18B20) sind notwendig für einen sicheren Betrieb der Lüftungsanlage. Bei niedrigen Außentemperaturen kann ansonsten der Wärmetauscher durch Frost zerstört werden.

Die Temperatursensoren sind an die Platine anschließen. Im Sourcecode ist die Variable serialDebug = 1 setzten und auf den Arduino flashen. Im seriellen Monitor werden die Temperaturen bei Änderung angezeigt. Für eine Temperaturänderungen können die Sensoren in die Hand genommen werden. Temperaturen von -127.0 zeigen, dass der Sensor nicht gefunden wurde.

Wenn die Temperatursensoren in der Anlage verbaut und verkabelt sind, sollte die korrekte Zuordnung zu den Luftströmen überprüft werden. Bei einer Außentemperatur von 5°C und einer Wohnraumtemperatur von 22 °C hat die Außenluft (T1) die geringste Temperatur, etwa 8 °C, anhängig von den baulichen Gegebenheiten. Die Zuluft (T2) wird bei etwa 18°C liegen. Die Abluft (T3) wird bei etwa 21°C und die Fortluft (T4) bei etwa 10°C liegen (T1 < T4 < T2 < T3). Wird diese Reihenfolge nicht eingehalten, es entweder die Außentemperatur sehr hoch oder die Zuordnung der Temperatursensoren zu den Luftströmen ist nicht korrekt.

## Lüfter

Da die Lüfter üblicherweise mit Netzspannung betrieben werden, ist besondere Vorsicht und Fachkenntnis notwendig.

Die Lüfter sind mit Netzspannung versorgen und an die Platine anschließen. Im Sourcecode die Variable serialDebugFan = 1 setzten und in der UserConfig.h #define DEBUG definieren, kompilieren und den Arduino flashen. Im seriellen Monitor werden die Drehzahlen bei Änderung angezeigt. Hier sollte überprüft werden, dass das Tachosignal der Lüfter korrekt erkannt wird (siehe auch 6.5.1).

Für den erfolgreichen Betrieb der Lüftungsanlage ist die korrekte Drehzahlerkennung die Voraussetzung.

### Überprüfung des Tachosignals vom Lüfters

Bei der Inbetriebnahme hat sich die korrekte Erkennung des Tachosignals als nicht immer einfach herausgestellt. Die Firma Pluggit hat während der Bauzeit der Anlage AP300 unterschiedliche Lüfter verbaut. Die Tachosignale der Lüfter haben sich als „unterschiedlich“ gut herausgestellt. Ob die Erkennung korrekt funktioniert, kann mit dem Python-Tool plotfans.py grafisch überprüft werden.

https://github.com/svenjust/room-ventilation-system/Docs/debug_fans/plotfans.py

Hinweise siehe: https://github.com/svenjust/room-ventilation-system/issues/11

Das Skipt plotfans.py stellt die Werte der Soll-, Istdrehzahl und PWM Signal der Lüfter grafisch dar. Das Script benötigt die „mqtt-Logausgabe“ der Lüfter. Um eine Logausgabe für die Lüfter mit Soll-, Istdrehzahl und PWM Signal zu bekommen ist das folgende Vorgehen erforderlich:

Die Software für den Arduino muss mit #define DEBUG kompiliert werden. Die Übertragung muss für jeden Lüfter muss einzeln aktiviert werden.

mosquitto_pub -t d15/debugset/kwl/fan1/getvalues -m on
mosquitto_pub -t d15/debugset/kwl/fan2/getvalues -m on

Die übertragenen Werte können mit der folgenden Zeile in einer Datei "/tmp/debug.log" protokolliert werden:

mosquitto_sub -v -h localhost -t "d15/debugstate/#" > /tmp/debug.log

Die Werte aus der Datei "/tmp/debug.log" können durch das Script plotfans.py dargestellt werden. Im Verzeichnis /tmp werden zwei Dateien mit der grafischen Darstellung der Drehzahlen von Lüfter 1 und 2 angelegt.

python <Pfad zu Script>\plotfans.py --infile /tmp/debug.log --out /tmp

Der folgende Aufruf zeigt die weiter möglichen Aufrufparameter:

python <Pfad zu Script>\plotfans.py -h zeigt die Aufrufparameter

Das folgende Bild zeigt im oberen Diagramm einen Lüfter mit fehlerhafter Tachosignalerkennung, die Schwankungen der Drehzahl (rpm: Revolution per minute) sind viel zu groß (600 bis etwa 1100 U/min bei gleichem PWM-Signal (ssf).

Im unteren Diagramm wird die Differenz zwischen der Solldrehzahl und der erkannten Istdrehzahl (GAP) dargestellt. Auch hier erkennt man die starken Schwankungen von 500 U/min (+/-250) bei gleichbleibenden PWM-Signal.

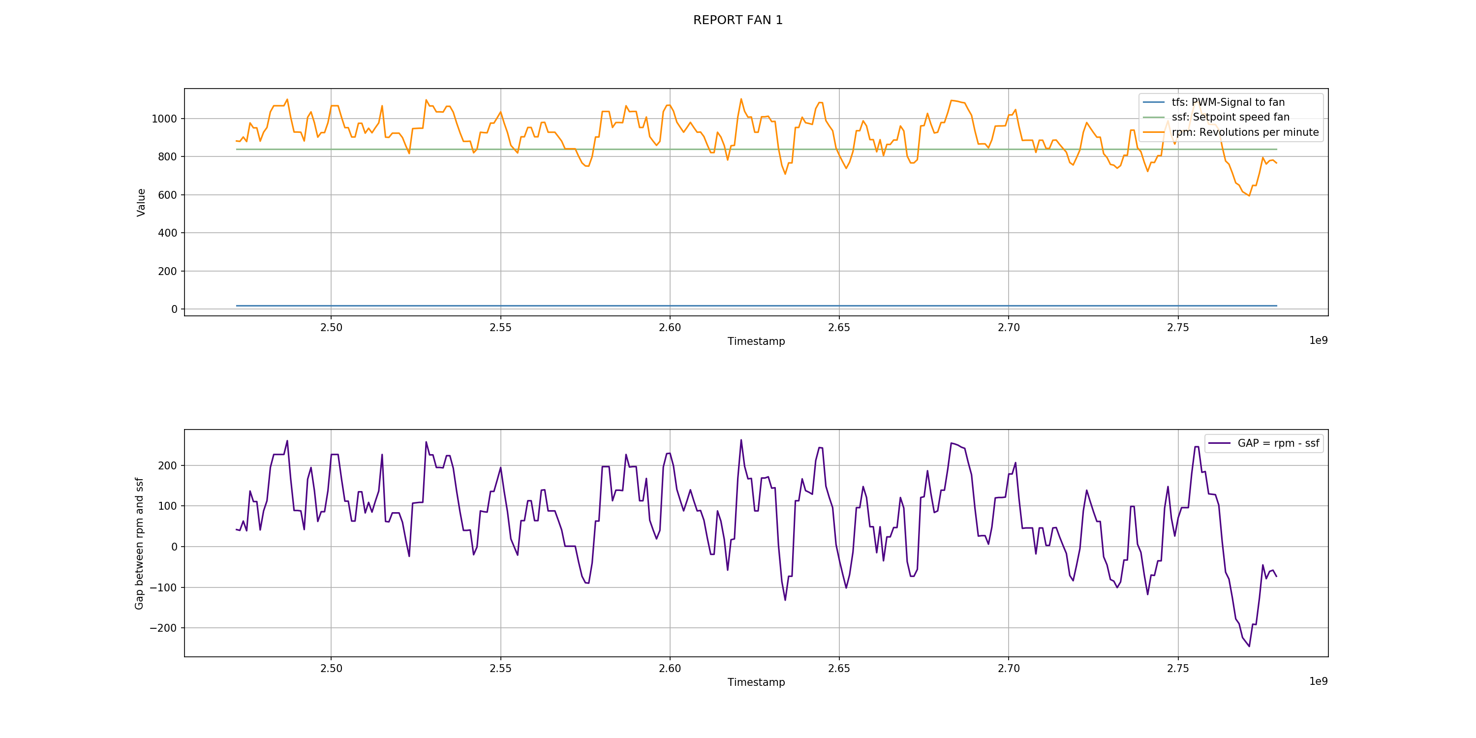
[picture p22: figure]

Abbildung 10: Fehlerhafte Erkennung des Tachosignals (rpm)

Eine korrekte Tachosignalerkennung zeigt das folgenden Bild. Die Linie rpm verläuft stetig mit kleinen Änderungen und im unteren Diagramm (GAP) sind keine „wilden“ Schwankungen zu erkennen, die Sprünge resultieren aus der Änderung der Solldrehzahl, hier während einer Kalibrierungsfahrt. Eine permanente Abweichung zwischen der Soll- und Istdrehzahl kann durch die Lüfterkalibrierung behoben werden.

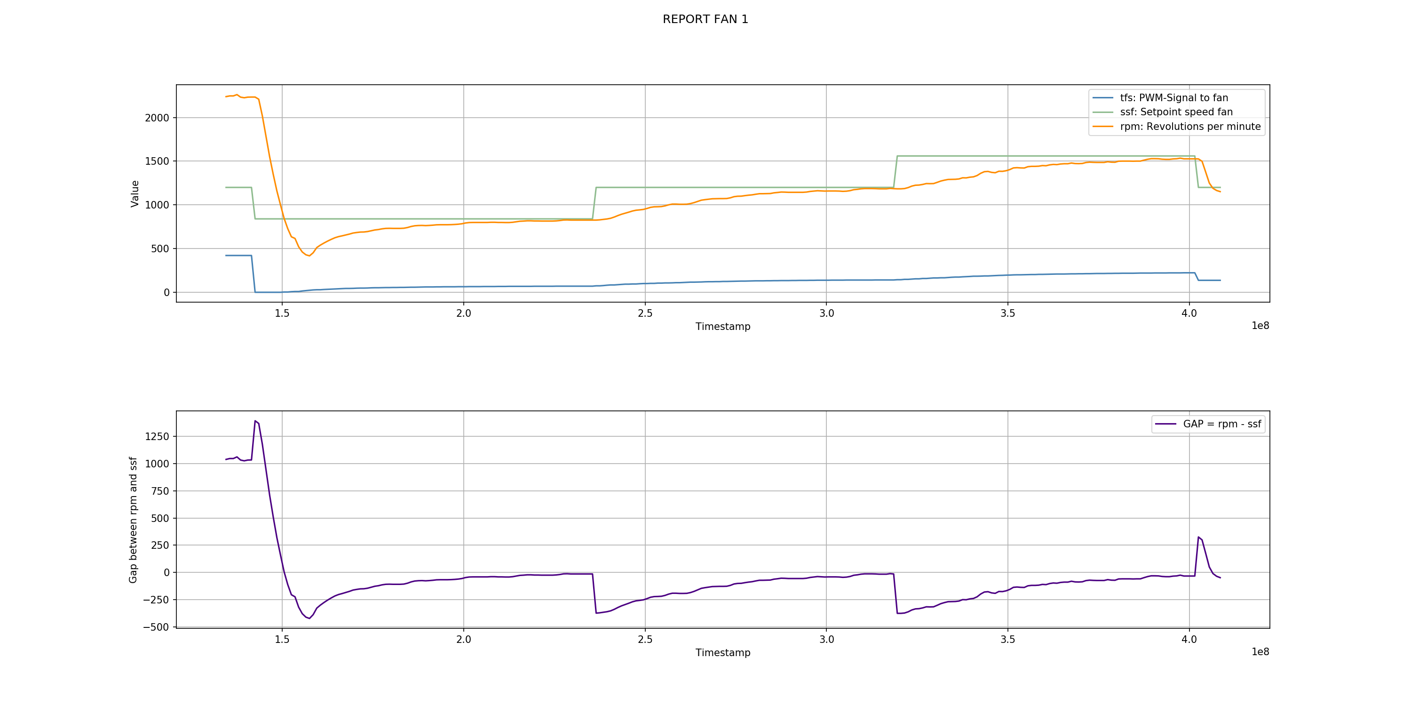
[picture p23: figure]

Abbildung 11: Korrekte Erkennung des Tachosignals (rpm)

Gründe für die fehlerhafte Erkennung können u.a. sein:

- Kalte oder fehlerhafte Lötstellen zum Tachosignal des Lüfters → Lötstellen auf Platine und Stecker überprüfen
- Unsauberes elektrisches Tachosignal zum Lüfter, Beurteilung mit Oszilloskop möglich → evtl. Pullup-Widerstand R11, R12 mit 4,7k und/oder Kondensator C1, C2 mit 100nF einbauen oder Änderung der Tachosignalerkennung zwischen FALLING und RISING (KWLConfig.h: TachoSamplingMode), siehe auch https://www.arduino.cc/reference/en/language/functions/external-interrupts/attachinterrupt/

Vor der weiteren Inbetriebnahme ist unbedingt eine korrekte Erkennung der Tachosignals sicher zustellen.

### Überprüfung der Anzahl der Tachosignale pro Lüfterumdrehung

Die Tachos der Lüfter können eine unterschiedlich Anzahl von Tachoimpulsen pro Lüfterumdrehung senden. Üblicherweise senden die verbauten Lüfter einen Impuls pro Umdrehung. Ein Anhaltspunkt für den Wert kann dem Datenblatt des Lüfters entnommen werden.

Es sind die folgenden Einstellungen anzupassen: StandardFan1ImpulsesPerRotation und StandardFan2ImpulsesPerRotation.

### Einstellen der Lüfterstufen

In der Werkeinstellungen sind vier Lüftungsstufen definiert. Lüftungsstufe 0 ist aus, 1, 2, 3 sind mit jeweils 70,% 100%, bzw 130% Drehzahl der Standardlüftungsstufe definiert. 100% Drehzahl entspricht 1.550 U/min. Die Lüftungsstufen sollten getestet werden:

mosquitto_pub -t d15/set/kwl/lueftungsstufe -m 1
mosquitto_pub -t d15/set/kwl/lueftungsstufe -m 2
mosquitto_pub -t d15/set/kwl/lueftungsstufe -m 3

### Kalibrierung der Lüfteransteuerung

Wenn das Tachosignal korrekt erkannt wird, kann eine Kalibrierung der Lüfteransteuerung vorgenommen werden. Dabei werden die Lüfter in die Lüftungsstufen geschaltet und es werden die PWM-Signale gespeichert, die zur Erreichung der jeweiligen Drehzahlen erforderlich sind. Diese gespeicherten PWM-Signale werden bis zur nächsten Referenzfahrt verwendet.

mosquitto_pub -t d15/set/kwl/calibratefans -m YES

Die Kalibrierung dauert mehrere Minuten. Maximal wird eine Kalibrierung 10 Minuten (TIMEOUT_CALIBRATION) versucht, dabei darf jeder Schritt einer Lüftungsstufe maximal 5 Minuten (TIMEOUT_PWM_CALIBRATION) dauern. Wenn die Kalibierung nicht erfolgreich ist, bleiben die gespeicherten PWM-Werte unverändert.

## Optional: Sommer-Bypass

Wenn der Sommer-Bypass mit Netzspannung betrieben wird, ist besondere Vorsicht und Fachkenntnis beim elektrischen Aufbau notwendig.

Der Sommer-Bypass ist in der Grundeinstellung im Automatikbetrieb und die Klappe ist geschlossen. Die Betriebsart (Automatik/Manuell) wird im EEPROM gespeichert, ebenso wie die Klappenstellung im manuellen Betrieb.

Um das korrekte Öffnen und Schließen der Klappe in der manuellen Betriebsart zu überprüfen, muss der Sommer-Bypass in den Manuellen Betrieb gesetzt werden und die Klappe per MQTT-Befehl geöffnet und geschlossen werden.

Die folgenden Kommandos setzen die manuelle Betriebsart und öffnen die Klappe.

mosquitto_pub -t d15/set/kwl/summerbypass/mode -m manual
mosquitto_pub -t d15/set/kwl/summerbypass/flap -m open

Bis zum Schalten der Bypass-Klappe können bis zu 6 Minuten vergehen, nach dem die erforderlichen Bedingungen vorliegen.

Das folgende Kommando schließt die Klappe, die Verzögerung kann ebenfalls wieder bis zu sechs Minuten betragen:

mosquitto_pub -t d15/set/kwl/summerbypass/flap -m close

Wenn die Klappe in der manuellen Betriebsart korrekt gefahren wurde, kann der Automatikbetrieb überprüft werden. Der Sommer-Bypass öffnet im Automatikbetrieb, wenn die folgenden Bedingungen erfüllt sind:

1. Die Außenlufttemperatur ist höher als TempAussenluftMin (13°C)
2. Die Ablufttemperatur ist höher als TempAbluftMin (24°C)
3. Die Ablufttemperatur ist 2 Grad höher als die Außenlufttemperatur
4. Der Bypass wurde in den letzten HystereseMinutes (60) Minuten nicht geschlossen.

Die Werkseinstellungen für den Sommer-Bypass entsprechen den am Markt anzutreffenden Anlagen.

Für das Testen des Bypasses sind die Temperatursensoren zu entfernen. Es ist ausreichend, die Datenleitungen der Sensoren vom Arduino zu lösen. Die Software für den Arduino muss mit #define DEBUG kompiliert werden. Anschließend können die Betriebsart und die Temperaturwerte über den MQTT-Broker in die Steuerung geschrieben werden.

mosquitto_pub -t d15/set/kwl/summerbypass/mode -m auto
mosquitto_pub -t d15/debugset/kwl/aussenluft/temperatur -m 14
mosquitto_pub -t d15/debugset/kwl/abluft/temperatur -m 26

Der Sommer-Bypass sollte jetzt geöffnet werden.

Die Fahrdauer kann mit der Variablen intervalBypassSummerSetFlaps im Sourcecode angepasst werden.

## Optional: Vorheizregister

Das Vorheizregister wird automatisch bei drohender Vereisung aktiviert. Für das Testen des Bypasses sind die Temperatursensoren zu entfernen. Es ist ausreichend, die Datenleitungen der Sensoren vom Arduino zu lösen. Die Software für den Arduino muss mit #define DEBUG kompiliert werden. Anschließend können per mqtt die folgenden Temperaturen vorgegeben werden. Das Vorheizregister sollte jetzt heizen. ACHTUNG: Das Vorheizregister darf nur im Luftstrom betrieben werden.

mosquitto_pub -t d15/debugset/kwl/fortluft/temperatur -m 1
mosquitto_pub -t d15/debugset/kwl/aussenluft/temperatur -m -1.1

# Einstellungen im Betrieb

Alle mqtt-Topics sind in der Datei https://github.com/svenjust/room-ventilation-system/tree/master/Docs/mqtt%20topics/mqtt_topics.ods (https://github.com/svenjust/room-ventilation-system/tree/master/Docs/mqtt%20topics/mqtt_topics.ods) dokumentiert, ebenso deren Implementierungsstatus. In der Datei sind auch kurze Erläuterung zu den Topics.

Für das Mitlesen aller mqtt-Meldungen der Lüftungsanlage sind zwei Subscribes notwendig:

mosquitto_sub -v -h localhost -t d15/state/
mosquitto_sub -v -h localhost -t d15/debugstate/

Für das Mitlesen des debugstate muss die Software für den Arduino mit #define DEBUG kompiliert werden.

## Setzen der Lüftungsstufe

mosquitto_pub -t d15/set/kwl/lueftungsstufe -m <Nr der Lüftungsstufe>

## Steuerung der Bypass-Klappe

Um die Bypass-Klappe manuell zu steuern muss sie in den manuellen Betriebsmodus geschaltet werden.

mosquitto_pub -t d15/set/kwl/summerbypass/mode -m manual

Anschließend kann die Bypass-Klappe geöffnet bzw. geschlossen werden.

mosquitto_pub -t d15/set/kwl/summerbypass/flap -m open
mosquitto_pub -t d15/set/kwl/summerbypass/flap -m close

# Bedienung mit Touch-Display

Doku offen...

# Einbindung dieser Steuerung in fhem

Für die Einbindung ist ein mqtt Broker erforderlich, siehe Abschnitt 6.3. Im fhem muss ein Device für die Verbindungen zum mqtt Broker erstellt werden.

define myBroker MQTT 192.168.20.240:1883 ## bitte EIGENE IP-Adresse eintragen

Anschließend muss ein Device für die Lüftungsanlage erstellt werden:

define kwl MQTT_DEVICE
attr kwl IODev myBroker
attr kwl publishSet 0 1 2 3 d15/set/kwl/lueftungsstufe
attr kwl room DEV_KWL
attr kwl stateFormat transmission-state
attr kwl subscribeReading_Fan1Speed d15/state/kwl/fan1/speed
attr kwl subscribeReading_Fan2Speed d15/state/kwl/fan2/speed
attr kwl subscribeReading_StateLueftungsstufe d15/state/kwl/lueftungsstufe
attr kwl subscribeReading_Temp01Aussenluft d15/state/kwl/aussenluft/temperatur
attr kwl subscribeReading_Temp02Zuluft d15/state/kwl/zuluft/temperatur
attr kwl subscribeReading_Temp03Abluft d15/state/kwl/abluft/temperatur
attr kwl subscribeReading_Temp04Fortluft d15/state/kwl/fortluft/temperatur

# Bauteillisten

## Arduino, LAN-Modul, Temperatursensoren, 4-fach Relais

Basisteile
Beschreibung | Bauelement | Alternative | Anzahl
Temperatursensoren | DS18B20 im Edelstahlgehäuse | | 4
Microcontroller | Arduino Mega R3 | | 1
LAN | LAN Shield W5100 | | 1
Relaisboard | 4 fach Relais Arduino für Sommer-Bypass und Lüfter | | 1
optional: 4 fach DAC 0-10V für das Vorheizregister | https://www.horter-shop.de/de/home/93-bausatz-i2c-analog-input-modul-5-kanal-10-bit-4260404260752.html | | 1
optional: DHT22 Luftfeuchtesensoren, für Abluft- und ggfs Zuluftstrom | DHT22 | | 2
optional: VOC Sensor, z.B. Figaro TGS2600 | TGS2600 | | 1
optional: CO2-Sensor, z.B. MH-Z14 | MH-Z14 | | 1

## Interface Board P300

P300_IF
Bezeichnung auf Board | Beschreibung | Bauelement | Alternative | Anzahl
J1 | 6 poliger Verbinder zu Relais Board 2,5mm Pinabstand | JST XH2.54 XH 2,54mm, 6-polig | Molex_KK-254 AE-6410-06A 1x06_P2.54mm_Vertical | 1
J2 | 3 poliger Verbinder zu DHT1 2,5mm Pinabstand | JST XH2.54 XH 2,54mm, 3-polig | Molex_KK-254 AE-6410-03A 1x03_P2.54mm_Vertical | 1
J3 | 3 poliger Verbinder zu DHT2 2,5mm Pinabstand | JST XH2.54 XH 2,54mm, 3-polig | Molex_KK-254 AE-6410-03A 1x03_P2.54mm_Vertical | 1
J4 | 8 poliger Verbinder zu Lüftern 2,5mm Pinabstand, MOLEX ist PINKOMPATIBEL | Molex_KK-254 AE-6410-06A 1x08_P2.54mm_Vertical | JST XH2.54 XH 2,54mm, 8-polig | 1
J5 | 3 poliger Verbinder zu DS18B20 2,5mm Pinabstand | JST XH2.54 XH 2,54mm, 3-polig | Molex_KK-254 AE-6410-03A 1x03_P2.54mm_Vertical | 1
J6 | 3 poliger Verbinder zu DS18B20 2,5mm Pinabstand | JST XH2.54 XH 2,54mm, 3-polig | Molex_KK-254 AE-6410-03A 1x03_P2.54mm_Vertical | 1
J7 | 3 poliger Verbinder zu DS18B20 2,5mm Pinabstand | JST XH2.54 XH 2,54mm, 3-polig | Molex_KK-254 AE-6410-03A 1x03_P2.54mm_Vertical | 1
J8 | 3 poliger Verbinder zu DS18B20 2,5mm Pinabstand | JST XH2.54 XH 2,54mm, 3-polig | Molex_KK-254 AE-6410-03A 1x03_P2.54mm_Vertical | 1
J9 | 2 poliger Verbinder zu 12V Versorgung 2,5mm Pinabstand, nur notwendig bei Horter DAC oder analogem Druckboard | JST XH2.54 XH 2,54mm, 2-polig | Molex_KK-254 AE-6410-03A 1x02_P2.54mm_Vertical | 1
J10 | 4 poliger Verbinder zu analogem Druckboard 2,5mm Pinabstand | JST XH2.54 XH 2,54mm, 4-polig | Molex_KK-254 AE-6410-03A 1x04_P2.54mm_Vertical | 1
J11 | 3 poliger Verbinder zu VOC TGS2600 2,5mm Pinabstand | JST XH2.54 XH 2,54mm, 3-polig | Molex_KK-254 AE-6410-03A 1x03_P2.54mm_Vertical | 1
J12 | 4 poliger Verbinder I2C 2,5mm Pinabstand | JST XH2.54 XH 2,54mm, 4-polig | Molex_KK-254 AE-6410-03A 1x04_P2.54mm_Vertical | 1
J13 | 4 poliger Verbinder zu MH-Z Serial2 2,5mm Pinabstand | JST XH2.54 XH 2,54mm, 4-polig | Molex_KK-254 AE-6410-03A 1x04_P2.54mm_Vertical | 1
J14 | 2 poliger Verbinder zu 5V Versorgung 2,5mm Pinabstand | JST XH2.54 XH 2,54mm, 2-polig | Molex_KK-254 AE-6410-03A 1x02_P2.54mm_Vertical | 1
J15, J16 | 8 poliger Verbinder zu Display 2,5mm Pinabstand | JST XH2.54 XH 2,54mm, 8-polig | | 2
R1 - R4 | Widerstand 4.7k | Resistors_THT:R_Axial_DIN0207_L6.3mm_D2.5mm_P2.54mm_Vertical | | 4
R5, R6 | Widerstand 220 | Resistors_THT:R_Axial_DIN0207_L6.3mm_D2.5mm_P2.54mm_Vertical | | 2
R7 - R10 | Widerstand 4.7k | Resistor_THT:R_Axial_DIN0207_L6.3mm_D2.5mm_P2.54mm_Vertical | | 4
R11, R12 | Widerstand 4,7k | Resistors_THT:R_Axial_DIN0207_L6.3mm_D2.5mm_P2.54mm_Vertical | | 2
U1, U2 | Optokoppler PC817 | Package_DIP:DIP-4_W7.62mm | | 2
C1, C2 | Kondensator 100nF | Capacitors_THT:C_Disc_D5.0mm_W2.5mm_P5.00mm | | 2
ICSP | 2x3 ICSP Female Stackable Header | 2x3 ICSP Female Stackable Header | | 1
PinHeader | 1x8 Female Stackable Header | 1x8 Female Stackable Header | | 4
PinHeader | 1x8 Pinheader | 1x8 Pinheader | | 2
PinHeader | 2x18 Pinheader | 2x18 Pinheader | | 1

## Display Board

Display board
Bezeichnung auf Board | Beschreibung | Bauelement | Alternative | Anzahl
J1, J2 | 8 poliger Verbinder zu Display 2,5mm Pinabstand | JST XH2.54 XH 2,54mm, 8-polig | Kabel direkt ohne Stecker löten | 2

## Spannungsversorgung und 230V Lüfteranschluss

HiVolt
Bezeichnung auf Board | Beschreibung | Bauelement | Alternative | Anzahl
F1 | 250V T 4A | Fuse:Fuseholder_TR5_Littlefuse_No560_No460 | | 1
J1 | 230V Eingang – Molex kompatibel mit Pluggit | Connector_Molex:Molex_Mini-Fit_Jr_5566-02A_2x01_P4.20mm_Vertical | | 1
J2 | 230V Verbindung zu Lüftern – Molex kompatibel zu Pluggit | Connector_Molex:Molex_Mini-Fit_Jr_5566-08A_2x04_P4.20mm_Vertical | | 1
J3, J4 | Stiftleiste 6P | Connectors_Terminal_Blocks:TerminalBlock_bornier-6_P5.08mm | | 2
J5 | 12V | Connector_Molex:Molex_KK-254_AE-6410-02A_1x02_P2.54mm_Vertical | | 1
J6 | 5V | Connector_Molex:Molex_KK-254_AE-6410-02A_1x02_P2.54mm_Vertical | | 1
RV1 | JNR-10D431K | Varistor:RV_Disc_D12mm_W7.5mm_P7.5mm | ~ | 1
T1 | HLK-PM12 | HLK-PM12 | | 1
T2 | 5V Schaltnetzteil | Meanwell IRM-05-5 (NOTWENDIG BEI DISPLAY) | HLK-PM05 ohne Display | 1

# Bilder der verwendeten Hardware

## Arduino Mega 2560REV3

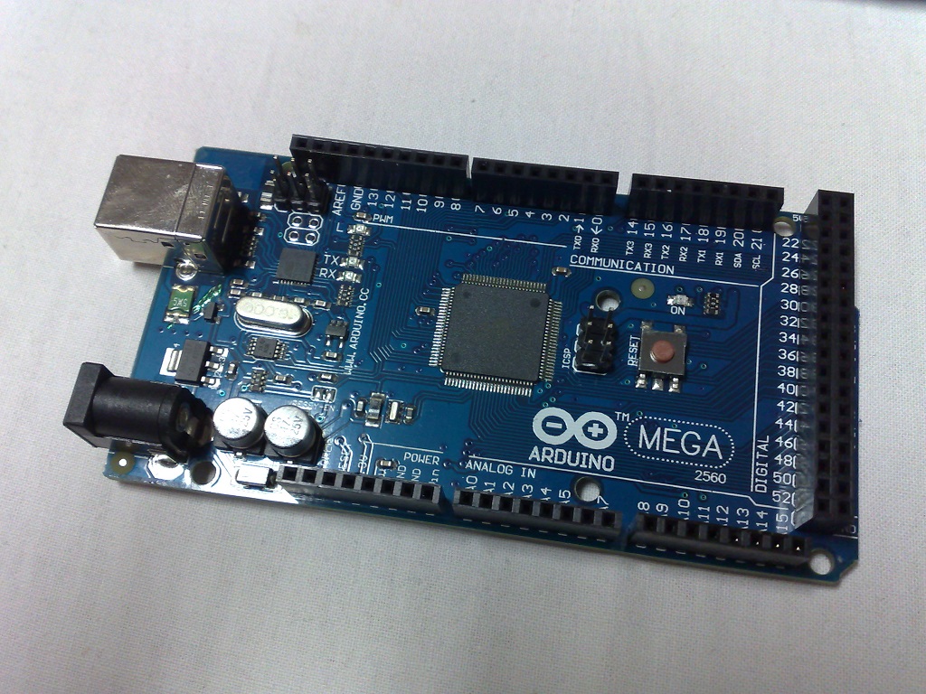
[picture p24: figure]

Abbildung 12: Arduino Mega 2560 REV
Bild von Dsimic - Eigenes Werk, CC BY-SA 4.0, https://commons.wikimedia.org/w/index.php?curid=35850081

## LAN Shield mit W5100

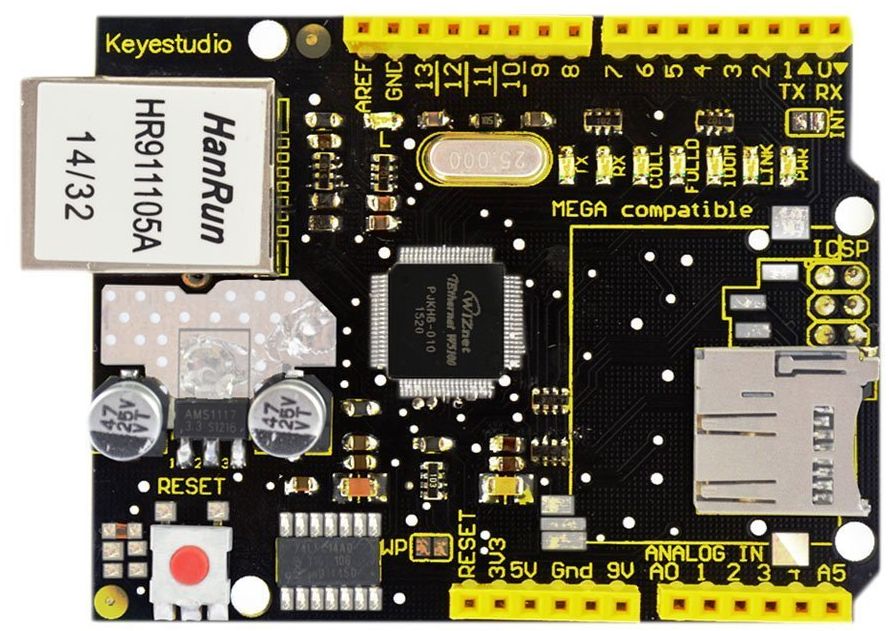
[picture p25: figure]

## Relais Shield


## DAC von Horter


## Temperatursensoren DS18B20


## Touch-Display 3,5“, mcufriend-Library, Auflösung 480x320


Wichtig ist, dass das Display auf das LAN Shield gesteckt werden kann, die Pins also an den beiden Längsseiten und nicht unten an der Querseite hat.

https://github.com/svenjust/room-ventilation-system Seite 32

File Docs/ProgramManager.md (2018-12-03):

# Program Manager

The ventilation system supports programming ventilation mode based on time of day
and weekday. A network connection, MQTT broker and a NTP server is a prerequisite,
so you need to configure at least NetworkIPAddress, NetworkMQTTBroker and
NetworkNTPServer in UserConfig.h.

## Programs and Program Sets

The program manager manages programs, which contain start and end time, ventilation
mode to use for this time and two sets of flags - weekdays and program set flags.
Further, the program manager manages up to 8 program sets, which can be selected
by writing a single value (e.g., a set for regular use and another set for vacation
period).

Weekdays flags indicate, whether a program is considered for the given weekday or
not.

Program set flags indicate whether a program is considered for the given program
set or not.

Program data and current program set index are stored in EEPROM, so they survive
a power outage.

## Program Selection

The program selection runs periodically and simply checks each program in the list.
If a program matches (i.e., the program is enabled and the current time is in the
time range of the program, including weekday check), then this program is considered.
The controller then picks matching program with the **highest index**.

With this, you can store more generic programs at lower indices and fine-tune with
more precise programs at higher indices.

## Program String

A program is defined by a string in the form:

        HH:MM HH:MM F wwwwwww pppppppp

where:
* HH:MM HH:MM are start and stop times,
* F is ventilation mode to set (typically 0-3),
* wwwwwww are flags for weekdays indicating whether to run the program on
  a given weekday (1) or not (0),
* pppppppp are flags for program sets in which this program is enabled (1)
  for this set or not (0).

## MQTT Communication

To communicate with the program manager, use the following MQTT messages:

Message                         | Value            | Description
------------------------------- | ---------------- | ------------------------
`d15/set/kwl/program/##/data`   | program string   | Set program data.
`d15/set/kwl/program/##/enable` | program set mask | Enable or disable a program for program sets.
`d15/set/kwl/program/##/get`    | (ignored)        | Send program info back for one program or all, if ## is `all`.
`d15/set/kwl/program/set`       | program set idx  | Activate given program set (0-7).

When setting a program, weekday flags and enabled flag are optional. If weekdays
are not set, the program will be considered every day. If enabled flag is not
set, the program will be by default enabled.

The controller sends back the following status information:

Message                           | Value            | Description
--------------------------------- | ---------------- | ------------------------
`d15/state/kwl/program/##/data`   | program string   | Program data.
`d15/state/kwl/program/##/enable` | program set mask | Program enable mask for program sets.
`d15/state/kwl/program/index`     | ##               | Currently running program index or -1 if none running.
`d15/state/kwl/program/set`       | program set idx  | Currently used program set (0-7).

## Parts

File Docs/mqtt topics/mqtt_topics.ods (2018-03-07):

 | EindeutigeBezeichnungClient/set/...(dann z.B. wie in FHEM üblich)
 | EindeutigeBezeichnungClient/state/...(dann z.B. wie in FHEM üblich)
 | Prefix | state oder set |  |  |  | Topic | Implementiert? | Wert EEPROM | Speicherplatz | Erläuterung | Werte
 | d15/ | state/ | kwl/ | heartbeat |  | d15/state/kwl/heartbeat | ja |  |  | Heartbeart der Lüftungsanlage, Lebenszeichen alle 30 Sekunden | online/offline
KONFIGURATIONSEINSTELLUNGEN und AKTUELLE WERTE
 | d15/ | set/ | kwl/ | getconfig |  | d15/set/kwl/getconfig | FEHLT |  |  | KWL antwortet mit allen Konfigurationseinstellungen
 | d15/ | set/ | kwl/ | getvalues |  | d15/set/kwl/getvalues | ja |  |  | KWL antwortet mit allen Messwerten
 | d15/ | set/ | kwl/ | resetAll_IKNOWWHATIMDOING |  | d15/set/kwl/resetAll_IKNOWWHATIMDOING | ja |  |  | Alle in der KWL im EEPROM gespeicherten Werte und Einstellungen werden resettet, anschliessend wird neu gestartet | YES
 | d15/ | set/ | kwl/ | calibratefans |  | d15/set/kwl/calibratefans | ja |  |  | Das PWM Signal für beide Lüfter wird kalibiriert. | YES
TEMPERATUREN und SENSOREN
 | d15/ | set/ | kwl/ | temperatur/ | gettemp | d15/set/kwl/temperatur/gettemp | ja |  |  | Befehl: KWL liefert die Temperaturen der Tempertursensoren fr Außenluft, Zuluft, Abluft und Fortluft
 | d15/ | state/ | kwl/ | aussenluft/ | temperatur | d15/state/kwl/aussenluft/temperatur | ja |  |  | Rückmelden der Temperatur für den Zulufttemperatursensor | Außenluft
 | d15/ | state/ | kwl/ | zuluft/ | temperatur | d15/state/kwl/zuluft/temperatur | ja |  |  |  | Zuluft
 | d15/ | state/ | kwl/ | abluft/ | temperatur | d15/state/kwl/abluft/temperatur | ja |  |  |  | Abluft
 | d15/ | state/ | kwl/ | fortluft/ | temperatur | d15/state/kwl/fortluft/temperatur | ja |  |  |  | Fortluft
 | d15/ | state/ | kwl/ | antifreeze |  | d15/state/kwl/antifreeze | ja |  |  |  | Status Frostschutz | preheating, fan1off
 | d15/ | set/ | kwl/ | antifreeze/ | hysterese | d15/set/kwl/antifreeze/hysterese | ja | x | 12 |  | Hysterese Temperatur (Standard 3K)
 | d15/ | state/ | kwl/ | dht1/ | temperatur | d15/state/kwl/dht1/temperatur | ja |  |  | Rückmelden der Temperatur für den DHT1
 | d15/ | state/ | kwl/ | dht1/ | humidity | d15/state/kwl/dht1/humidity | ja |  |  | Rückmelden der Temperatur für den DHT2
 | d15/ | state/ | kwl/ | dht2/ | temperatur | d15/state/kwl/dht2/temperatur | ja |  |  | Rückmelden der Luftfeuchtigkeit für den DHT1
 | d15/ | state/ | kwl/ | dht2/ | humidity | d15/state/kwl/dht2/humidity | ja |  |  | Rückmelden der Luftfeuchtigkeit für den DHT2
 | d15/ | state/ | kwl/ | abluft/ | co2 | d15/state/kwl/abluft/co2 | ja |  |  | Rückmelden der CO2 in Abluft
 | d15/ | state/ | kwl/ | abluft/ | voc | d15/state/kwl/abluft/voc | ja |  |  | Rückmelden der VOC in Abluft
 | d15/ | state/ | kwl/ | effiencyKwl |  | d15/state/kwl/effiencyKwl | ja |  |  | Rückmelden der berechneten Wirkungsgrades
FEHLER
 | d15/ | state/ | kwl/ | error/ | temperatursensoren | d15/state/kwl/error/temperatursensoren |  |  |  | true, wenn nicht alle vier Temperatursensoren gefunden wurden
LÜFTUNGSSTUFE
 | d15/ | set/ | kwl/ | lueftungsstufe |  | d15/set/kwl/lueftungsstufe | ja |  |  | Befehl: KWL soll Stufe einstellen | Stufe 1-n (abhängig Definition SourceCode)
 | d15/ | state/ | kwl/ | lueftungsstufe |  | d15/state/kwl/lueftungsstufe | ja |  |  | Die eingestellte Lüftungsstufe
VENTILATORENDREHZAHL
 | d15/ | set/ | kwl/ | fans/ | calculatespeed | d15/set/kwl/fans/calculatespeed | ja |  |  | Definiert, wie das PWM Signal berechnet wird | PID oder PROP | PID = PID-Regler PROP=Proportional zur Nromdrehzahl
 | d15/ | set/ | kwl/ | fans/ | getspeed | d15/set/kwl/fans/getspeed | ja |  |  | Befehl: KWL liefert die Geschwindigkeiten für Fan 1 und 2
 | d15/ | set/ | kwl/ | fan1/ | standardspeed | d15/set/kwl/fan1/standardspeed | ja | x | 2 | Befehl: Setzen der Normdrehzahl für Fan1 in Stufe 3 | Fan1=Abluftvent.
 | d15/ | state/ | kwl/ | fan1/ | speed | d15/state/kwl/fan1/speed | ja |  |  | aktuelle Drehzahl Fan1 | U/min
 | d15/ | set/ | kwl/ | fan2/ | standardspeed | d15/set/kwl/fan2/standardspeed | ja | x | 4 | Befehl: Setzen der Normdrehzahl für Fan2 in Stufe 3 | Fan1=Zuluftvent.
 | d15/ | state/ | kwl/ | fan2/ | speed | d15/state/kwl/fan2/speed | ja |  |  | aktuelle Drehzahl Fan2 | U/min
SOMMER-BYPASS
 | d15/ | set/ | kwl/ | summerbypass/ | getvalues | d15/set/kwl/summerbypass/getvalues | ja |  |  | liefert die states im Bereich summerbypass | auto/manual
 | d15/ | set/ | kwl/ | summerbypass/ | mode | d15/set/kwl/summerbypass/mode | ja | x |  | Automatik oder manueller Betrieb des Bypasses. Bei manuellem Betrieb erfolgt die Steuerung der Bypass-Klappe nur über flap | auto/manual
 | d15/ | state/ | kwl/ | summerbypass/ | mode | d15/state/kwl/summerbypass/mode | ja
 | d15/ | set/ | kwl/ | summerbypass/ | flap | d15/set/kwl/summerbypass/flap | ja | x |  | Bei manuellem Bypass wird hiermit das Öffnen/Schliessen der Klappe gesteuert. Bei Automatik hat die Einstellung keine Auswirkung | open/close
 | d15/ | state/ | kwl/ | summerbypass/ | flap | d15/state/kwl/summerbypass/flap | ja
 | d15/ | set/ | kwl/ | summerbypass/ | TempAbluftMin | d15/set/kwl/summerbypass/TempAbluftMin | ja | x | 6 | Heißt bei Pluggit TMax
 | d15/ | state/ | kwl/ | summerbypass/ | TempAbluftMin | d15/state/kwl/summerbypass/TempAbluftMin | ja
 | d15/ | set/ | kwl/ | summerbypass/ | TempAussenluftMin | d15/set/kwl/summerbypass/TempAussenluftMin | ja | x | 8 | Heißt bei Pluggit TMin
 | d15/ | state/ | kwl/ | summerbypass/ | TempAussenluftMin | d15/state/kwl/summerbypass/TempAussenluftMin | ja
 | d15/ | set/ | kwl/ | summerbypass/ | HystereseMinutes | d15/set/kwl/summerbypass/HystereseMinutes | ja | x | 10 | Minuten bis zum frühesten Öffnen/Schliessen der Klappe, 0=diesen Wert nicht beachten
 | d15/ | state/ | kwl/ | summerbypass/ | HystereseMinutes | d15/state/kwl/summerbypass/HystereseMinutes | ja
FEUERSTÄTTEN-MODUS
 | d15/ | set/ | kwl/ | heatingapp/ | combinedUse | d15/set/kwl/heatingapp/combinedUse |  |  |  | Wenn Kamin / raumluftabhängiger Ofen vorhanden, dann YES, KWL schaltet bei Frost für 4 Stunden aus | YES / NO | Standard: NO
 | d15/ | state/ | kwl/ | heatingapp/ | combinedUse | d15/state/kwl/heatingapp/combinedUse |  |  |  |  | YES / NO
DEBUG
 | d15/ | debugset/ | kwl/ | fan1/ | getvalues | d15/debugset/kwl/fan1/getvalues | ja |  |  | Schaltet Debugmessages zum Lüfter 1 ein/aus | on/off
 | d15/ | debugset/ | kwl/ | fan2/ | getvalues | d15/debugset/kwl/fan2/getvalues | ja |  |  | Schaltet Debugmessages zum Lüfter 2 ein/aus | on/off
 | d15/ | debugstate/ | kwl/ | fan1 |  | d15/debugstate/kwl/fan1 | ja |  |  | Debugmeldungen zum Lüfter 1
 | d15/ | debugstate/ | kwl/ | fan2 |  | d15/debugstate/kwl/fan2 | ja |  |  | Debugmeldungen zum Lüfter 2
 | Die folgenden Topics sind nur für die SW-Entwicklung, es werden Messwerte überschrieben, es kann damit der Sommer-Bypass und die Frostschutzschaltung getestet werden
 | d15/ | debugset/ | kwl/ | aussenluft/ | temperatur | d15/debugset/kwl/aussenluft/temperatur | ja |  |  | DEBUG: Aussentemperatur
 | d15/ | debugset/ | kwl/ | zuluft/ | temperatur | d15/debugset/kwl/zuluft/temperatur | ja |  |  | DEBUG: Zulufttemperatur
 | d15/ | debugset/ | kwl/ | abluft/ | temperatur | d15/debugset/kwl/abluft/temperatur | ja
 | d15/ | debugset/ | kwl/ | fortluft/ | temperatur | d15/debugset/kwl/fortluft/temperatur | ja

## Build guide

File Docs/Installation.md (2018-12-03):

# System Installation

TODO document general installation

## Setting up MQTT Communication Prefix

In order to set up MQTT communication, you need to configure at least NetworkIPAddress
and NetworkMQTTBroker in UserConfig.h (see KWLConfig.h for details).

By default, MQTT topics use prefix `d15` to address the system. You can change this
in several ways:
* Initially by setting PrefixMQTT in UserConfig.h to your prefix.
* At runtime by sending a value to topic `d15/set/kwl/install/prefix`.

The setting is stored in EEPROM, so it will be available after a restart. Currently,
the prefix is limited to 7 characters.

The documentation always refers to prefix `d15`, you need to replace it with your
user-defined prefix.

Setting the prefix allows to run multiple ventilation systems in one network, but
more importantly, to run one real system and one for experimentation, but still
connected to the same network and same MQTT broker.

To differentiate clients, the client name is composed as `kwlClient:<prefix>`.
I.e., the default config would use `kwlClient:d15` as client name in MQTT broker.

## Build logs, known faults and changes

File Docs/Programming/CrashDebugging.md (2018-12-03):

# Debugging Crashes

## DeadlockWatchdog

The project uses DeadlockWatchdog library to detect deadlocks in the code.
These typically happen when stack overflows or dynamic allocation is used
and the heap overflows (e.g., due to fragmentation). But, there may be other
reasons, e.g., unresponsive code reading a sensor or serial communication
port (e.g., W5100 Ethernet driver, if no Ethernet shield present).

DeadlockWatchdog resets the microcontroller if it was not reset in time.
Currently, we use maximum value (8s), since there are tasks, which do take
1-2 seconds. When the timeout hits, the instruction pointer is determined
at which the watchdog interrupt was generated. This is typically in an
endless loop or similar.

## Getting Crash Information

Crash information of recent 4 crashes (as configured by KWLConfig::MaxCrashReportCount)
is stored in EEPROM in KWLPersistentConfiguration and can be queried from
there. Each crash report contains instruction pointer, stack pointer, real
time (if available) and millis() timer at the time of the crash.

Following MQTT topics can be used to evaluate crash information and to provoke
crashes and restarts:

Topic                                | Value | Description
------------------------------------ | ----- | --------------------
`d15/debugset/kwl/crash/getvalues`   | (any) | Request to send crash reports.
`d15/debugset/kwl/crash/resetvalues` | (any) | Request to clear all crash reports.
`d15/debugset/kwl/crash/provoke_IKNOWWHATIMDOING` | `YES` | Provoke a deadlock and crash for testing purposes.
`d15/set/kwl/restart`                | `YES` | Restart the controller immediately.

Following MQTT Topics are used to communicate crash information:

Topic                         | Value          | Description
----------------------------- | -------------- | --------------------
`d15/state/kwl/statusbits`    | 0x########     | Bit 0x00040000 indicates crash presence.
`d15/debugstate/kwl/crash/##` | (crash report) | Describes crash report at slot ##.

Each crash report is formatted as follows: `ip XXXXXX sp XXX ntp ######### ms #########`.
Field IP contains instruction pointer in hexadecimal (byte address, not word
address), field SP contains stack pointer, field NTP contains seconds since
epoch of the crash (provided NTP is connected) and field MS contains value
of millis() at the time of crash.

Additionally, status bits of the system indicate crash report presence.

## Finding Code Location of the Crash

Now, the most interesting thing: how to find the code location.

First, you need to find your generated .elf file. To do that, you can turn on
verbose output during compilation in Arduino IDE preferences. When building, you
will see a line like this:

`"/Users/someone/Library/Arduino15/packages/arduino/tools/avr-gcc/4.9.2-atmel3.5.4-arduino2/bin/avr-objcopy" -O ihex -R .eeprom  "/var/folders/22/62g6566d6nbgvjvx_pp6499h0000gn/T/arduino_build_965557/KWLctl.ino.elf" "/var/folders/22/62g6566d6nbgvjvx_pp6499h0000gn/T/arduino_build_965557/KWLctl.ino.hex"`

The interesting thing is `/var/folders/22/62g6566d6nbgvjvx_pp6499h0000gn/T/arduino_build_965557/KWLctl.ino.elf`,
which is the generated ELF file containing the executable.

Now, you can disassemble the executable using avr-objdump like this:

`/Applications/Arduino.app/Contents/Java/hardware/tools/avr/bin/avr-objdump -d -S <path>/KWLctl.ino.elf >dump.txt`

This will produce `dump.txt`, where you can simply search for the instruction pointer
which caused the crash. Surrounding source code will give you the information about
where the crash happened.

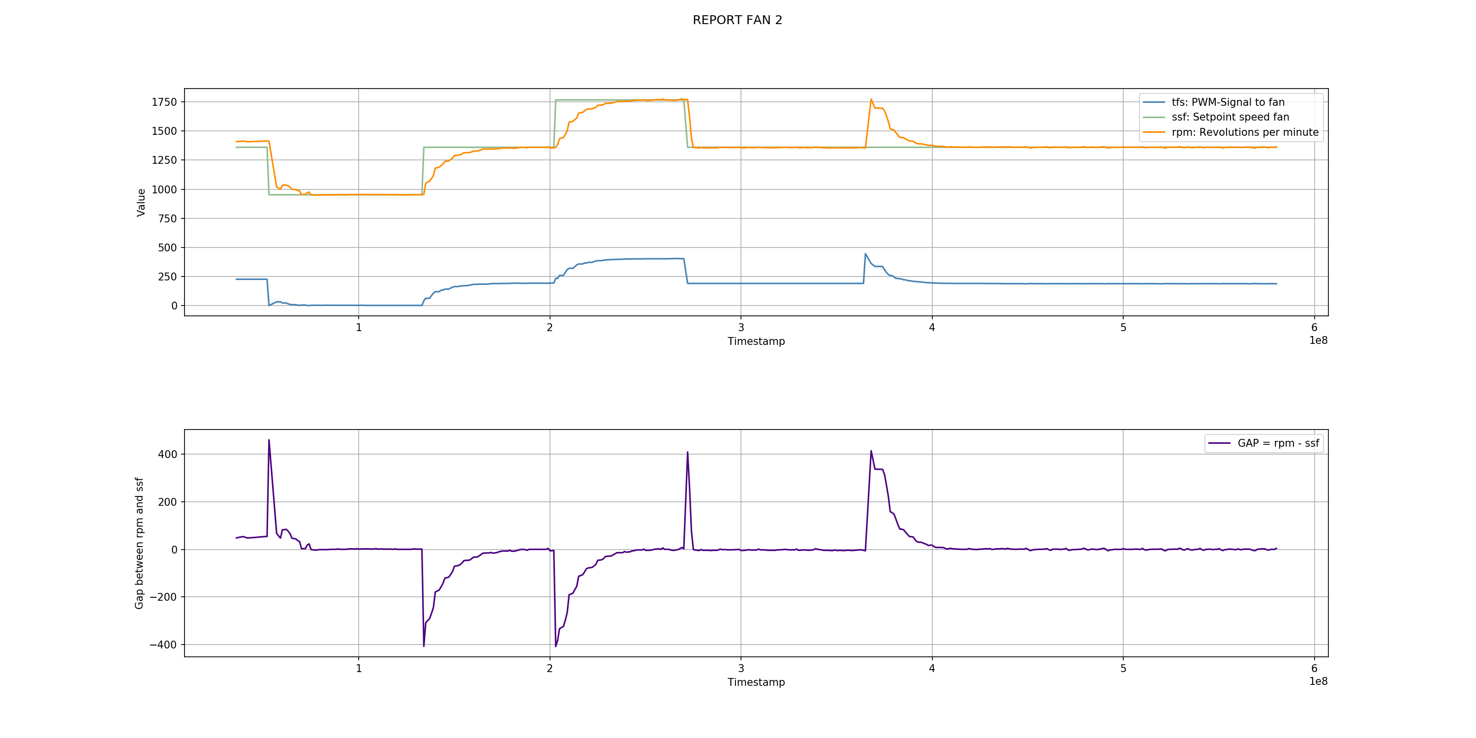
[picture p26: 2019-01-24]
Docs/debug_fans/example-debug/Plot_Fan2.png

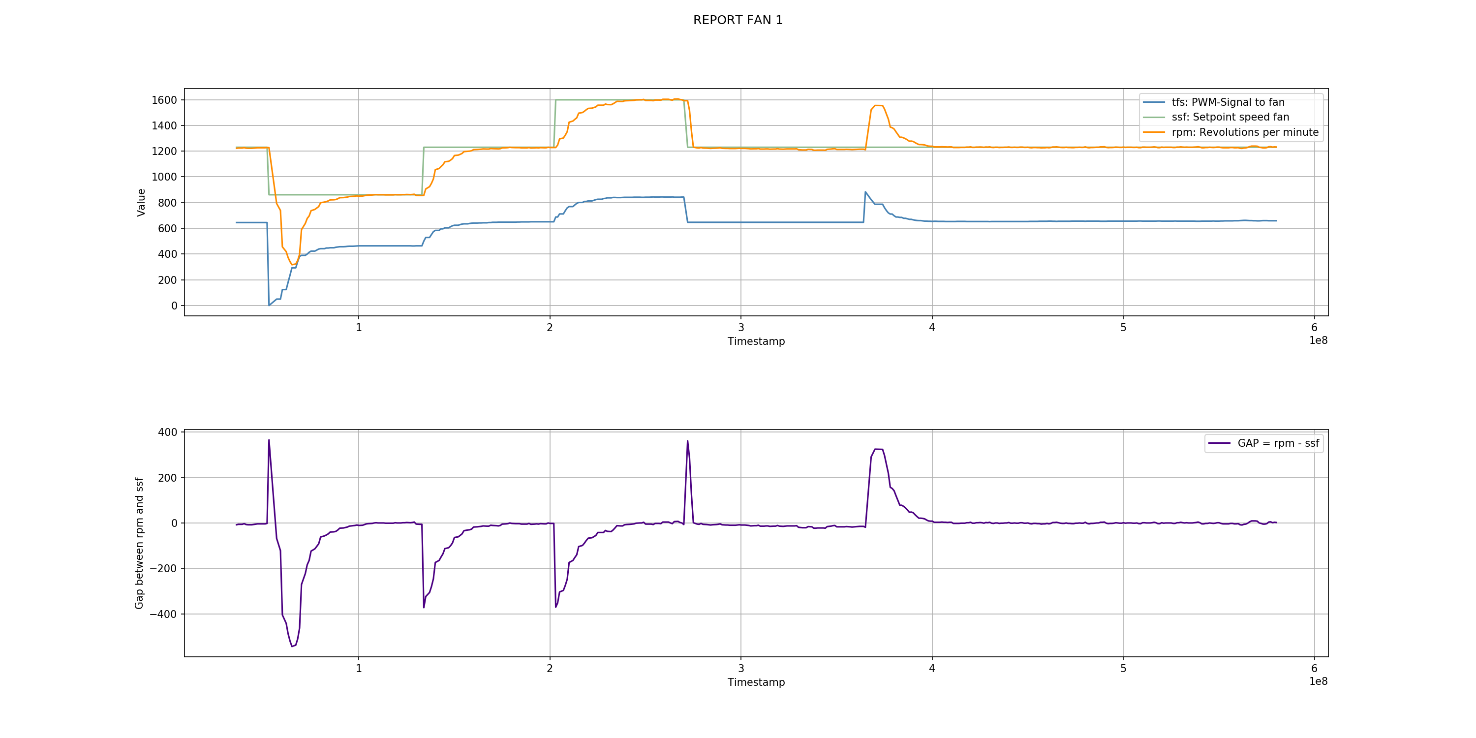
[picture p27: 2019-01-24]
Docs/debug_fans/example-debug/Plot_Fan1.png

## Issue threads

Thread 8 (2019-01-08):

Impulse pro Umdrehung für Tachosignal

svenjust, 2019-01-08:
In den Lüftungsanlagen sind unterschiedliche Lüfter verbaut. So ist die Pluggit P300 auch mit Lüftern der Serie r3g**225** (ansonsten wohl r3g**190**) ausgeliefert worden. Diese Lüfter liefern anscheinend 2 Impulse pro Umdrehung als Tachosignal. Die bisherige Implementierung geht von 1 Impuls pro Umdrehung aus.

Es soll in der Steuerung für die Lüfter ein Parameter PulsesPerRevolutionFan1 bzw. PulsesPerRevolutionFan2 ergänzt werden, der die Anzahl der Impulse am Tachosignal für eine Umdrehung des Lüfters enthält. Der Standardwert beider Parameter ist 1. Die Parameter sollen in der Datei UserConfig.h überschrieben werden können. Eine Änderung beider Parameter zur Laufzeit (am Display oder per mqtt) erscheint NICHT notwendig, die Parameter sind hardwareabhängig fest für eine Hardwarekonfiguration.

Referenz: https://forum.fhem.de/index.php/topic,83025.msg883495.html#msg883495 und https://www.ebmpapst.com/media/content/info-center/downloads_10/catalogs/compactfansen2011/compactfanssingle2011/DC-Luefter-Specials_2016_01_D.pdf

schreter, 2019-01-12:
FYI, working on it. The first untested version is at https://github.com/schreter/room-ventilation-system/commit/e268139ac739b8ff0973632512f22bae7331b40d.

Closed 2019-01-13.

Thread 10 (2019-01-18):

Error during compiling. 'class FanRPM' has no member named 'multiplier'

Jasimo, 2019-01-18:
Just tried to compile V.021, got the follwing error:
`FanControl.h:103:10: error: 'class FanRPM' has no member named 'multiplier'

     rpm_.multiplier() = static_cast<FanRPM::multiplier_t>(FanRPM::RPM_MULTIPLIER_BASE / ipr);

          ^

FanControl.h:103:45: error: 'multiplier_t' in 'class FanRPM' does not name a type

     rpm_.multiplier() = static_cast<FanRPM::multiplier_t>(FanRPM::RPM_MULTIPLIER_BASE / ipr);

                                             ^

FanControl.h:103:59: error: 'RPM_MULTIPLIER_BASE' is not a member of 'FanRPM'

     rpm_.multiplier() = static_cast<FanRPM::multiplier_t>(FanRPM::RPM_MULTIPLIER_BASE / ipr);

                                                           ^

'class FanRPM' has no member named 'multiplier'`

rgs
Jan

schreter, 2019-01-18:
Hi Jan,

FanRPM ist eine Lib. Arduino IDE macht leider kein Refesh (na ja, IMHO verdient es die Bezeichnung IDE gar nicht:)).

Ich nehme an, IDE schließen und neu öffnen sollte es beheben.

Ivan

Sent from my iPhone

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

Jasimo, 2019-01-18:
Hallo Ivan,

das hatte ich schon probiert, leider ohne Erfolg, komisch.

Gruß
Jan

schreter, 2019-01-18:
Hi Jan,

seltsam. Ich habe gerade probiert die neueste Version zu kompilieren und es ging ohne Probleme.

Hast du nur die drei Fehler oder auch weitere? Kann es sein, dass dein Arduino IDE zu alt oder "zu neu" ist? Ich habe 1.8.5.

Wie hast du die Libs installiert? Via link_libs.sh oder manuell kopiert (dann muss du Updates auch kopieren)?

Welches OS hast du für Entwicklung genutzt?

Gruss,

Ivan

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

Jasimo, 2019-01-18:
Ich nutze die 1.8.8.
Hatte die jedoch bei der vorherigen Version (die ohne die Apassung bezüglich Impulse pro Umdrehungen) auch genutzt, hatte geklappt. Nun hab ich ja scheinbar Lüfter verbaut die 2 Impulse pro Umdrehung machen und wollte die neue Version mal testen. Meine Lüfter zicken derzeit auch ein wenig bei der Kalibrierung.

Ich nutze das ganze unter Windows 10 ;-)
Die Bibliotheken hab ich ich der IDE installiert und die fehlenden kopiert. Muss ich vielleicht den Ordner FanRPM irgendwo hin kopieren?
Gruss
Jan

Closed 2019-01-18.

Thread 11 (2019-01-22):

PID Tuning parameters

Jasimo, 2019-01-22:
Hallo,
ich habe in meiner Pluggit P300 andere Lüfter verbaut es kommen bei mir zwei ebm-papst r3g225 ae19-12 zum Einsatz. Bei mir schlägt die Kalibrierung regelmäßig fehl, wenn ich es mit den folgenden Standard Parametern versuche:
```
static constexpr double aggKp  = 0.5,  aggKi = 0.1, aggKd  = 0.001;
static constexpr double consKp = 0.1, consKi = 0.1, consKd = 0.001;
```

senke ich diese Werte ab klappt die Kalibrierung, derzeit bin ich auf:
```
static constexpr double aggKp  = 0.25,  aggKi = 0.05, aggKd  = 0.001;
static constexpr double consKp = 0.05, consKi = 0.05, consKd = 0.001;
```

den Tipp bekam ich von Sven im FHEM-Forum, leider hab ich kein Oszilloskop um das vernünftig zu tunen, wie weit kann ich denn mit den Werten Kp, Ki, Kd runter, es scheint als ob es durch weiteres Absenken stabiler werden könnte.
Gruß
Jan

svenjust, 2019-01-22:
Hallo Jan!

> wie weit kann ich denn mit den Werten Kp, Ki, Kd runter

Im Prinzip beliebig weit, die Regelung der Lüfterdrehzahlen wird dann nur langsamer. Zu Bedeutung der Parameter siehe https://de.wikipedia.org/wiki/Regler

Zum Erreichen der Solldrehzahl werden bei einer Differenz von mehr als 1000 U/min zwischen der Soll- und Istdrehzahl die Parameter aggKp,  aggKi und aggKd verwendet. Wenn die Differenz kleiner als 1.000 U/min ist, dann werden die (kleineren) Parameter consKp, consKi, consKd verwendet. Ziel dabei ist, bei großer Differenz schnell die Solldrehzahl zu erreichen, siehe https://github.com/svenjust/room-ventilation-system/blob/b5b76cc4fead0a76dfd345f1fed9a546a3547fcd/Sourcecode/KWLctl/FanControl.cpp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

**NEU**: plotfans.py: Ein Script zur Visualisierung der Soll-, Istdrehzahl und PWM Signal der Lüfter. Das Script benötigt die Logausgabe der Lüfter, siehe https://github.com/svenjust/room-ventilation-system/blob/master/Docs/debug_fans/plotfans.py

Um eine Logausgabe für die Lüfter mit Soll-, Istdrehzahl und PWM Signal zu bekommen ist das folgende Vorgehen möglich:

Um die Logdatei zu erzeugen, muss die Software für den Controller mit dem `#DEBUG` kompiliert werden.

 Die Übertragung kann für jeden Lüfter einzeln aktiviert werden.
```
   mosquitto_pub -t d15/debugset/kwl/fan1/getvalues -m on
   mosquitto_pub -t d15/debugset/kwl/fan2/getvalues -m on
```

Die übertragenen Werte können mit der folgenden Zeile in einer Datei "/tmp/debug.log" protokolliert werden:
`   mosquitto_sub -v -h localhost -t "d15/debugstate/#" > /tmp/debug.log`

Die Werte aus der Datei "/tmp/debug.log" können durch das Script plotfans.py dargestellt werden.

AUFRUF: `python <Pfad zu Script>\plotfans.py --infile /tmp/debug.log --out /tmp`
`python <Pfad zu Script>\plotfans.py -h` zeigt die Aufrufparameter

VG Sven

Jasimo, 2019-01-22:
Hallo Sven,
ich debugge die Werte dann wärend einer Kalibrierung oder im normalen PROP Betrieb?
Könnte man nicht in den Code etwas wie PIDAutotune implementieren um die Werte für den verbauten Lüfter herauszubekommen?
https://playground.arduino.cc/Code/PIDAutotuneLibrary
Gruß Jan

Jasimo, 2019-01-22:
hier die Grafen der Fans, Anlage lief auf Stufe1
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

Jasimo, 2019-01-22:
Das ist ja das komische, die Lüfter schwanken hörbar und optisch überhaupt nicht. An der PWM Frequenz kann es auch nicht liegen, oder?

svenjust, 2019-01-22:
Lt. der Papst-Spec R3G225RE0703-BA-GER.pdf, Seite 9, sollen die Lüfter mit 1-10kHz PWM angesteuert werden. Der Arduino Mega verwendet per default 490 Hz, dieser Wert wird bisher nicht geändert. Ob dies ein Problem ist, weiß ich nicht.

Die Lüfter werden an Pin 44 und 46 mit dem PWM Signal versorgt. Auf dem Arduino Mega ist Timer 5 für die Steuerung zuständig, siehe http://sobisource.com/arduino-mega-pwm-pin-and-frequency-timer-control/

Du könntest versuchen, in der Datei KWLctl.ino, Zeile 75 den folgenden Code zu ergänzen:
` TCCR5B = (TCCR5B & 0xF8) | 0x02 ;  # Timer 5, Divisor 8, Frequency  3.921 KHz`

Neu kompilieren, Drehzahlen loggen und visualisieren.

Jasimo, 2019-01-22:
Hallo Sven,
ich mache das heute Abend mal, kaputt gehen kann da nix, oder?
Bin ja froh das die Kiste überhaupt wieder läuft ;-)
Gruß
Jan

svenjust, 2019-01-22:
Hallo Jan,
ich kann die Änderung erst heute Abend testen. Dann warte doch, bis ich heute Abend probiert habe, ich melde mich nachfolgend. Ich sehe mir die Änderung dann auch im Oszilloskop an, um sicher zu gehen, dass die Codeänderung auch eine Änderung der Frequenz bringt.

VG Sven

Jasimo, 2019-01-22:
so machen wir es.

svenjust, 2019-01-22:
Hallo Jan,

obige Codezeile führt zu der Frequenzänderung. Bitte in KWLctl.ino ergänzen, so dass es wie folgt aussieht:
`void setup()
{
  Serial.begin(57600); // Serielle Ausgabe starten

  // Timebase for PWM Signal
  TCCR5B = (TCCR5B & 0xF8) | 0x02 ; // Timer 5, Divisor 8, Frequency 3.921 KHz

  // *** TFT AUSGABE ***`

svenjust, 2019-01-22:
Vorher:
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

Nach Codeänderung: 3,93 kHz
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

Jasimo, 2019-01-22:
mit der Anpassung bekomme ich keine erfolgreiche Kalibrierung hin ;-(
Kommt nicht mal über Stufe1 in der Kalibrierung

Jasimo, 2019-01-22:
Ich bin glaube ich ein Stück weiter gekommen, eine Änderung von FALLING auf RISING brachte das folgende Ergebnis bei der Kalibrierung, wohlgemerkt wieder mit der standard PWM Frequenz des Arduino. Jedoch mit
```
static constexpr double aggKp  = 0.05,  aggKi = 0.01, aggKd  = 0.001;
static constexpr double consKp = 0.01, consKi = 0.01, consKd = 0.001;
```

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

svenjust, 2019-01-22:
Ich habe einen Lüfter der Anlage an meine Steuerung gehängt. Dann habe ich die folgenden Änderungen in der KWLctl.ino gemacht (ist eigentlich unwichtig, da der Standardwert eingestellt wird. Dies zeigt auch die Messung mit dem Oszilloskop:
```
  // Timebase for PWM Signal
  //TCCR5B = (TCCR5B & 0xF8) | 0x02 ; // Timer 5, Divisor 8, Frequency 3.921 KHz
  TCCR5B = (TCCR5B & 0xF8) | 0x03 ; // Timer 5, Divisor 64, Frequency 490.1 Hz            // default
  //TCCR5B = (TCCR5B & 0xF8) | 0x05 ; // Timer 5, Divisor 1024, Frequency 30.63 Hz
```
In der FanControl.cpp ist geändert:
```
static constexpr double aggKp  = 0.1,  aggKi = 0.1, aggKd  = 0.001;
static constexpr double consKp = 0.025, consKi = 0.01, consKd = 0.01;
```
Damit bekomme ich im Modus PID die folgenden Werte:
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

Aktuell weiß ich nicht, warum bei Dir die gemessene Drehzahl so schwankt. Die gemessene Drehzahl ist scheinbar der Grund für die nicht durchlaufende Kalibrierung.

VG Sven

svenjust, 2019-01-22:
Das sieht sehr gut aus! Das ist so korrekt.

Bezüglich der PWM Frequenz habe ich im Laufe des Abends auch die besten Erfahrungen mit der Standardfrequenz gemacht, etwa 490 Hz.

Das Triggern auf RISING hatte Ivan auch mal erwähnt, bei mir geht RISING und FALLING problemlos. Ich ändere aber im Sourcecode auf RISING. Die PID Parameter funktionieren bei mir auch, auch diese wandern in den master.

VG Sven

Jasimo, 2019-01-22:
Supi, Dir nochmals VIELEN DANK! Natürlich auch an Ivan. Zum Abschluß nochmal grafen im normalen Betrieb (Stufe2)
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

Gruß
Jan

svenjust, 2019-01-22:
Das sieht alles ok, top!

schreter, 2019-01-22:
Hi Jan,

Sorry, ich bin erst jetzt online. Aber, ich wollte auch vorschlagen, mit RISING vs. FALLING zu probieren. Freut mich zu hören, dass es jetzt tut und gut zu wissen, dass ich nicht der einzige bin, der das Problem hatte :-).

Bei mir waren die Messungen noch erratischer - ich hatte doppelte und manchmal dreifache Signale (im Bereich von Mikrosekunden). Hat mich auch in den Wahnsinn getrieben, bis ich es endlich durch trial and error rausgefunden hatte. Ich habe mittlerweile auch Filtering eingebaut, damit solche doppelte Spitzen rausgefiltert werden.Seitdem läuft es bei mir mit RISING zuverlässig, mit FALLING aber nicht - ich habe dann auch so erratische Messwerte. Möglicherweise fehlt irgendwo ein Filterkondensator oder so, ich bin da kein Experte.

Leider habe ich keinen brauchbaren Oszilloskop, nur so ein uraltes analoges Teil, daher ist es schwierig zu analysieren (mit Oszilloskop läuft es ja :-).

Gruss,

Ivan

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

Jasimo, 2019-01-23:
Ja, ich bin auch heilfroh das es nun läuft, vielleicht könnte man auf einem zukünfigen PCB schon mal etwas vorsehen für einen Kondensator, muss ja nicht zwingend bestückt werden, wenn es auch so läuft.
Jetzt kann ich mich endlich an das externe Display machen, das ist bei mir noch offen

svenjust, 2019-01-23:
> vielleicht könnte man auf einem zukünfigen PCB schon mal etwas vorsehen für einen Kondensator, muss ja nicht zwingend bestückt werden, wenn es auch so läuft.
Sicher kann ich den Kondensator bei neuen Platinen vorsehen. Ich stelle mir nur die Frage, ob er zu einer entscheidenden Glättung des Signals führt. Evtl. ist ein Pullup-Widerstand von 4,7k an der Tacholeitung und das Ausschalten des Arduino-internen Pullup-Widerstands besser geeignet. Da mein Lüfter bei RISING und FALLING vernünftige Signale liefert, bin ich hier auf Zuarbeit angewiesen.

In der Platine sehe ich Kondensator und Widerstand vor.

Closed 2019-01-22.

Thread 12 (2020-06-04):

Sommerbypass immer nur eine Stunde "open"

Jasimo, 2020-06-04:
Hallo,

gestern hatten wir hohe Temperaturen über 24 Grad im Haus, somit setzte die Automatik den Sommerbypass auf "open". Leider ist es "zumindest bei mir" so, dass dieser Zustand immer nur exakt eine Stunde auf "open" bleibt um dann wieder auf "closed" zu gehen. Obwohl die Abluft >24 Grad und die Außenluft <22 Grad war. Das hat die Steuerung gestern ein paar mal gemacht und es ist zu erkennen, dass er die Bypassklappe immer exakt für eine Stunde öffnet, diese dann wieder schließt obwohl die Temperaturen immer noch dafür Sorgen müssten, dass die Klappe offen bleibt.

Gruß

Jan

svenjust, 2020-06-05:
Hallo Jan,

vorab, ich habe aktuell meinen Testaufbau des Systems abbauen müssen, da ich meinen Schreibtisch zum Arbeiten (Homeoffice) benötige.

Ich schaue mir das Problem aber trotzdem zu gegebener Zeit gerne an, kann aber Herbst oder Winter werden… Falls Du selbst im Code suchen möchtest, SummerBypass.cpp ist der richtige Einstieg. Die Meldungen an der seriellen Schnittstelle, sollten zeigen was passiert.

Du kannst den Sommer-Bypass aber auch manuell über das TFT-Display einstellen. Damit könntest Du den Bypass im Sommer permanent geöffnet lassen.

VG Sven

Jasimo, 2020-06-05:
Hallo Sven,
danke für Deine Rückmeldung. Ich kann probieren mal nachzusehen, wobei meine Programmierkenntnisse beschränkt sind :-) Bis dahin steuere ich den Bypass manuell per FHEM in einem doif. Es wäre nur (irgendwann mal) toll wenn das auch autark funktioniert, falls FHEM mal offline ist.
Wenns denn überhaupt an der Steuerung liegt.

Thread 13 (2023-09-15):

Use for other ventilation

henfri, 2023-09-15:
Hello,

the control board of my Helios KWL 270Eco is broken.
I was now considering to replace it with your development. However, the Hardware is of course not compatible to it.

In the end, one only needs few connections:
- Temperature Sensors
- 1-10V and Speed signal
- bypass

So, I was wondering if you know any Arduino HAT that would be suitable?

Best regards,
HEndrik

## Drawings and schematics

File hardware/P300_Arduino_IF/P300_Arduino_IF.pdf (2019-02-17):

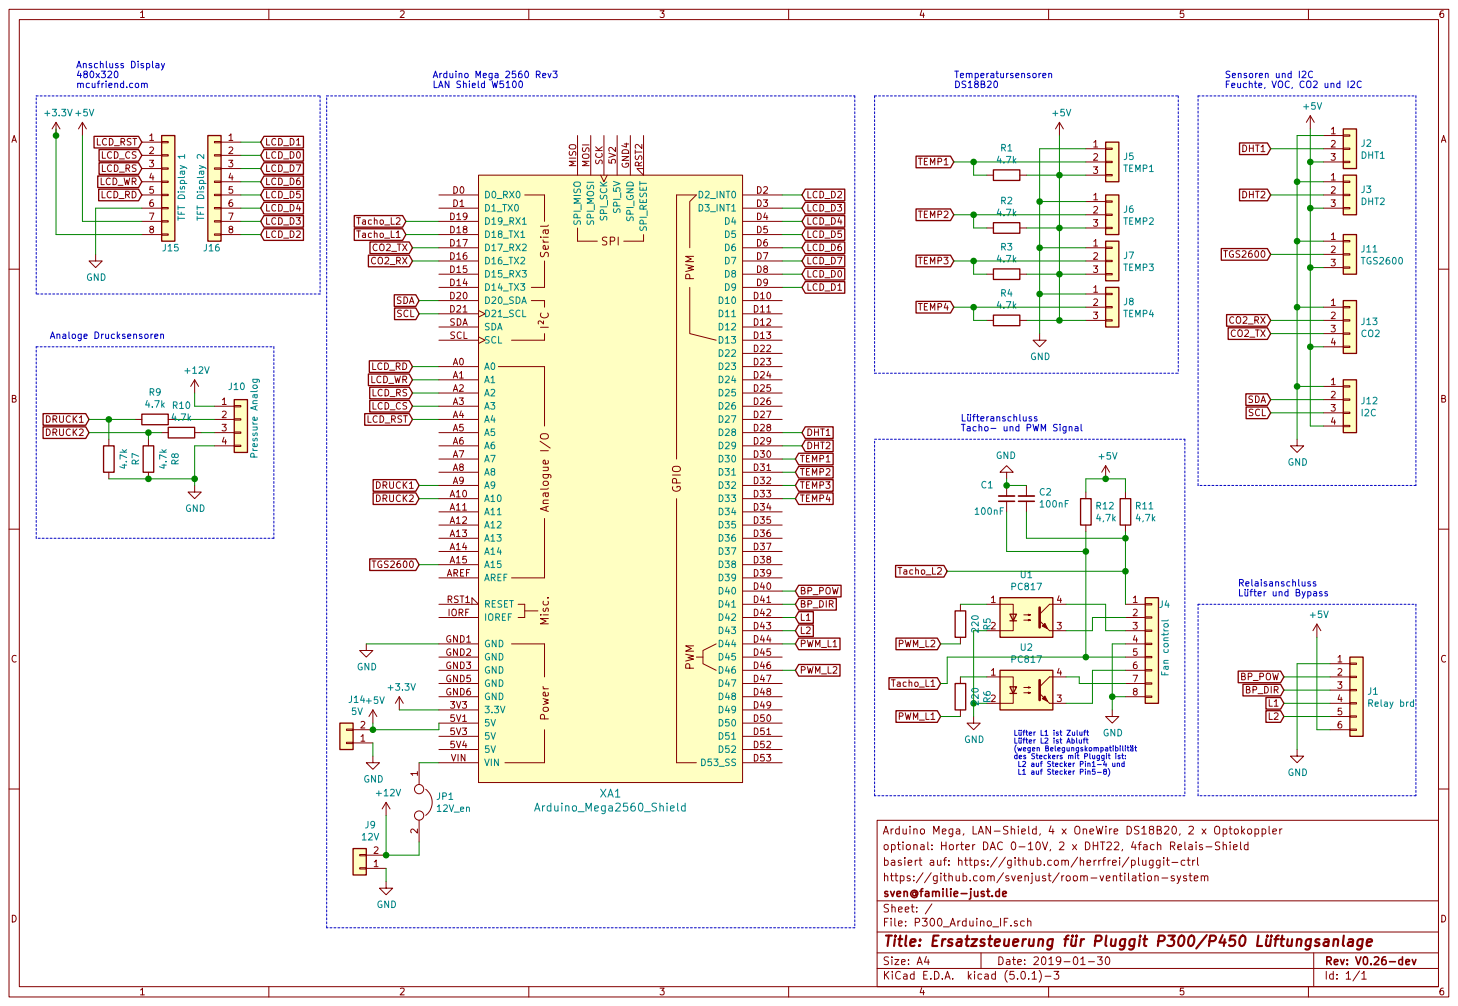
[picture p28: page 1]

Anschluss Display 480x320 mcufriend.com

Arduino Mega, LAN-Shield, 4 x OneWire DS18B20, 2 x Optokoppler 1

Lüfter L1 ist Zuluft Lüfter L2 ist Abluft (wegen Belegungskompatibilität des Steckers mit Pluggit ist:

optional: Horter DAC 0-10V, 2 x DHT22, 4fach Relais-Shield
basiert auf: https://github.com/herrfrei/pluggit-ctrl
https://github.com/svenjust/room-ventilation-system
File: P300_Arduino_IF.sch Sheet: / sven@familie-just.de

Id: 1/1 Title: Ersatzsteuerung für Pluggit P300/P450 Lüftungsanlage

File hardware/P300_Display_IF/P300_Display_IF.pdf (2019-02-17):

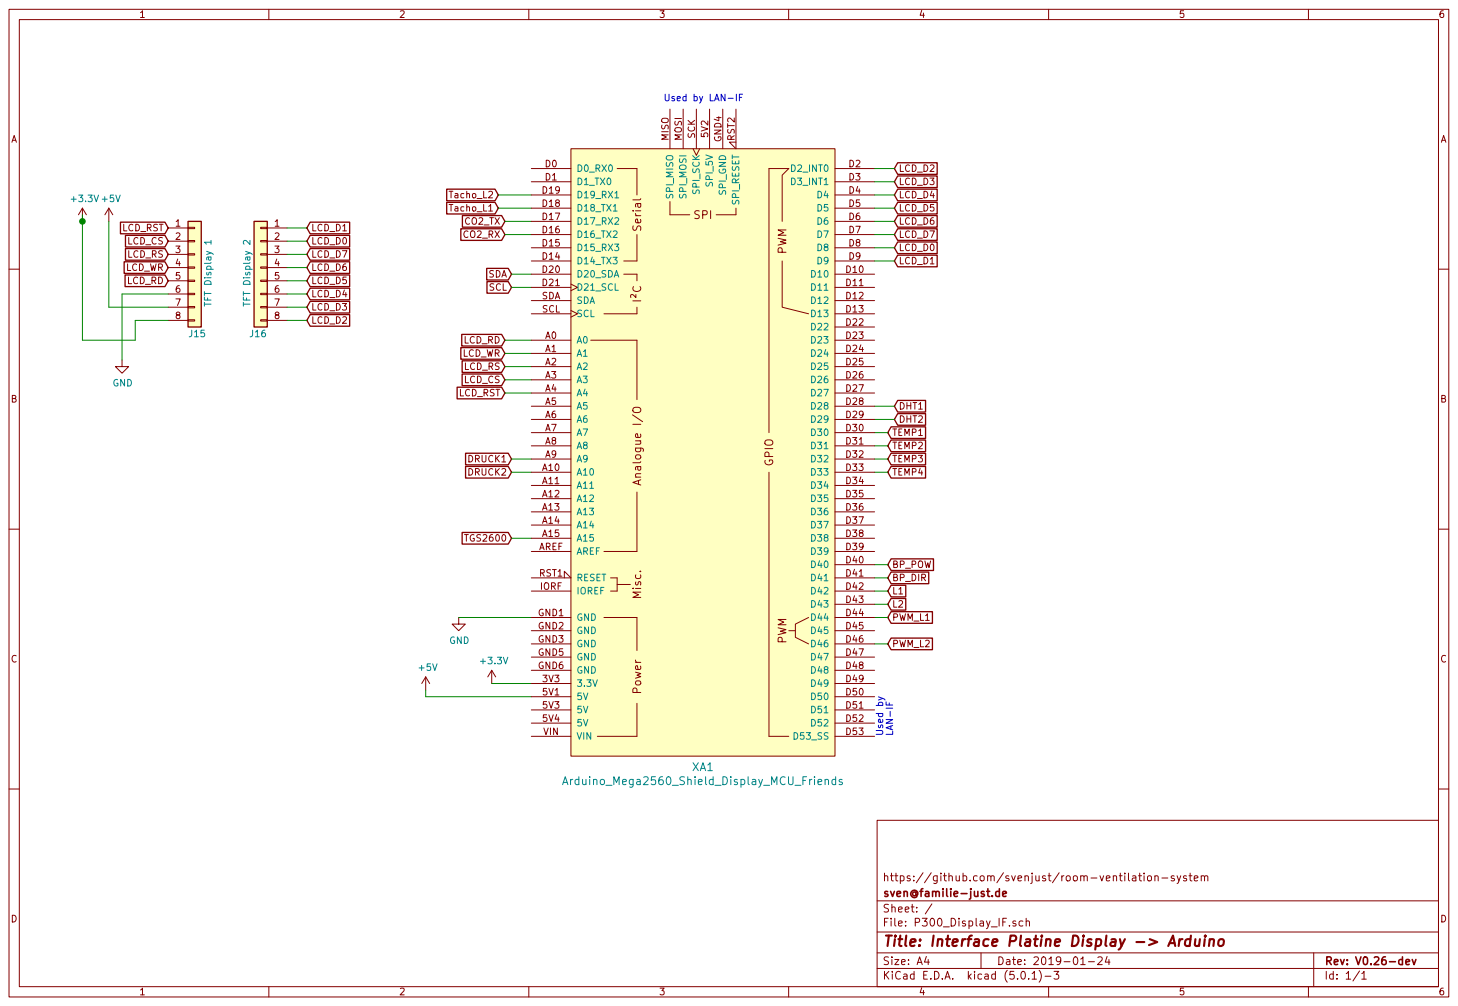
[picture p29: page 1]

Used by LAN-IF SDA

https://github.com/svenjust/room-ventilation-system
File: P300_Display_IF.sch Sheet: / sven@familie-just.de

Id: 1/1 Title: Interface Platine Display -> Arduino

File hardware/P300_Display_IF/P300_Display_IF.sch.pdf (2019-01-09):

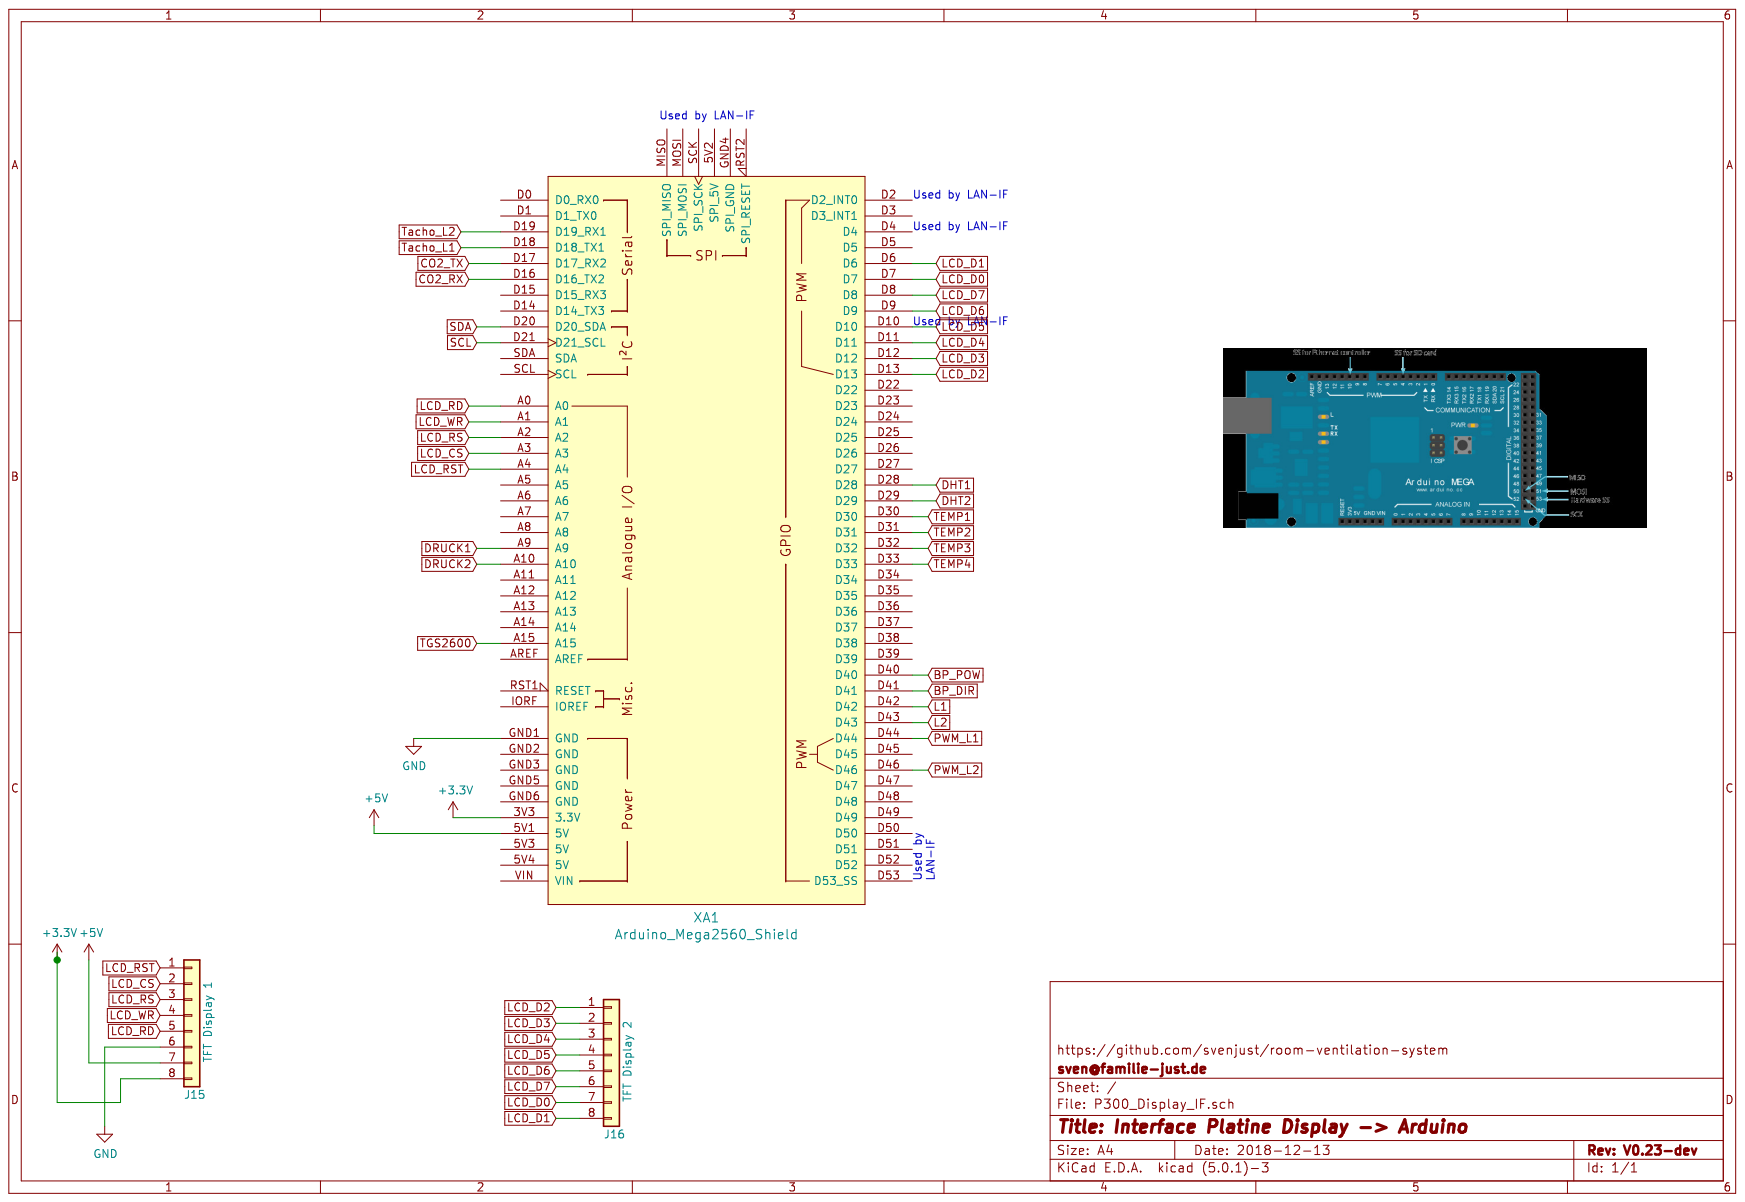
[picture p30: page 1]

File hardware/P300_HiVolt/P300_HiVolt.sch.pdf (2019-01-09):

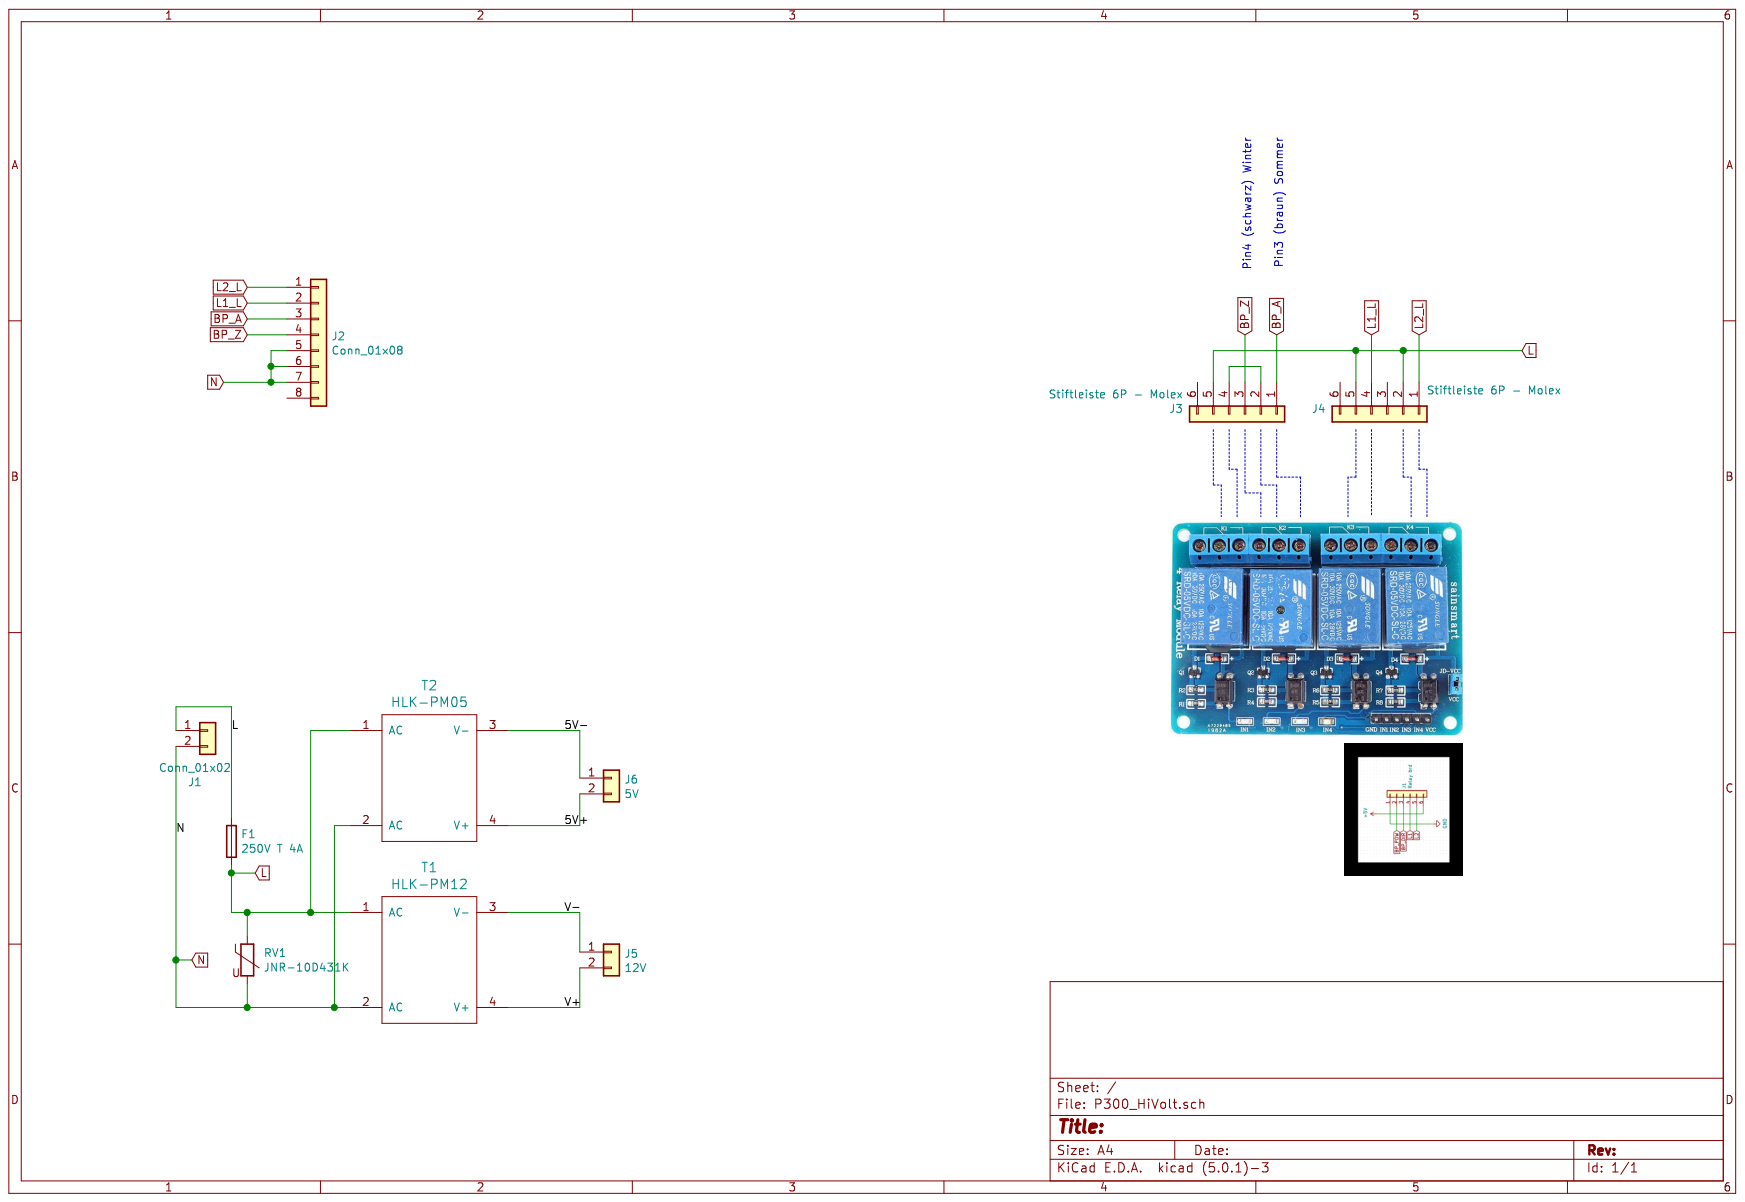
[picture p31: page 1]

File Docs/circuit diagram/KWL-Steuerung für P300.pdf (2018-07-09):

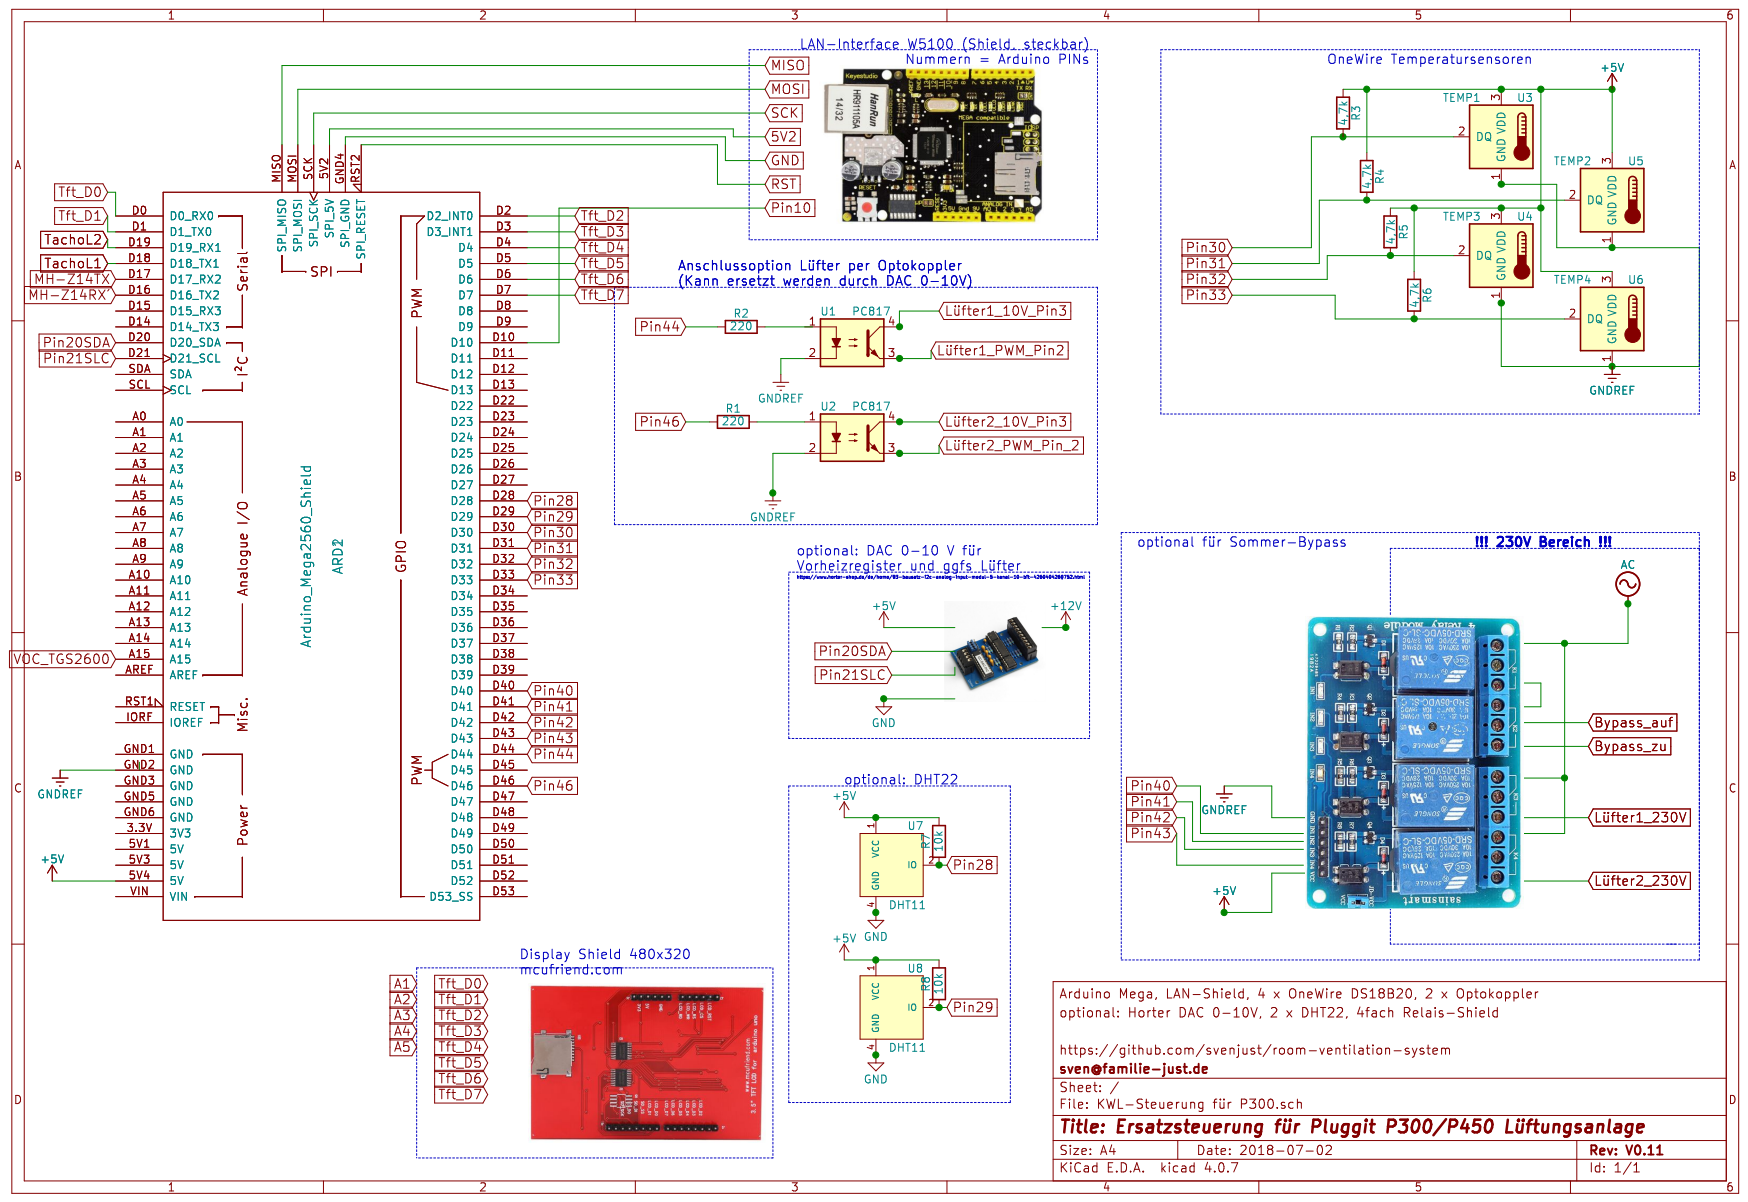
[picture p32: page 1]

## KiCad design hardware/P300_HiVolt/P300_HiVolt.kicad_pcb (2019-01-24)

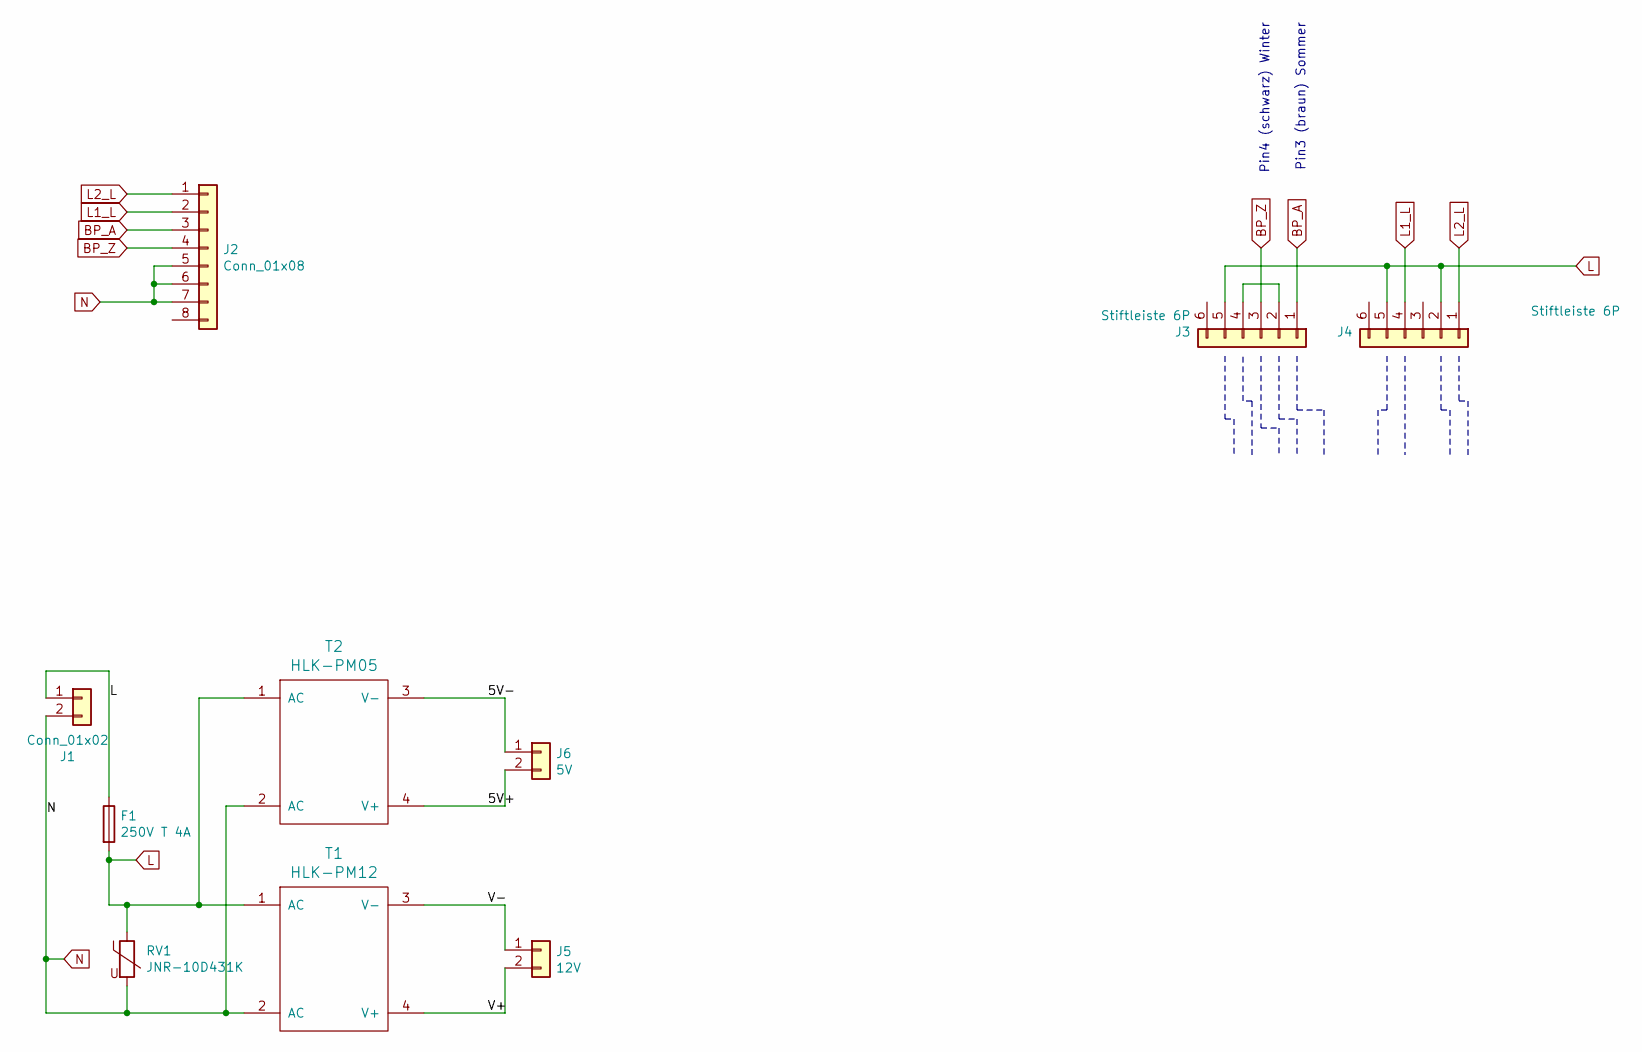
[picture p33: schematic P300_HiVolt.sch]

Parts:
F1: 250V T 4A; Fuseholder_TR5_Littlefuse_No560_No460
J1: Conn_01x02; Molex_Mini-Fit_Jr_5566-02A_2x01_P4.20mm_Vertical
J2: Conn_01x08; Molex_Mini-Fit_Jr_5566-08A_2x04_P4.20mm_Vertical
J3, J4: Stiftleiste 6P; TerminalBlock_bornier-6_P5.08mm
J5: 12V; Molex_KK-254_AE-6410-02A_1x02_P2.54mm_Vertical
J6: 5V; Molex_KK-254_AE-6410-02A_1x02_P2.54mm_Vertical
RV1: JNR-10D431K; RV_Disc_D12mm_W7.5mm_P7.5mm
T1: HLK-PM12
T2: HLK-PM05; HLK-PM12

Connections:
/5V+: J6.2, T2.4 (V+)
/5V-: J6.1, T2.3 (V-)
/V+: J5.2, T1.4 (V+)
/V-: J5.1, T1.3 (V-)
BP_A: J2.3, J3.1
BP_Z: J2.4, J3.3
L: F1.1, F1.2, J1.1, J3.5, J4.2, J4.5, RV1.1, T1.1 (AC), T2.1 (AC)
L1_L: J2.2, J4.4
L2_L: J2.1, J4.1
N: J1.2, J2.5, J2.6, J2.7, RV1.2, T1.2 (AC), T2.2 (AC)
unnamed: J3.2, J3.4

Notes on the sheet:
Pin3 (braun) Sommer
Pin4 (schwarz) Winter

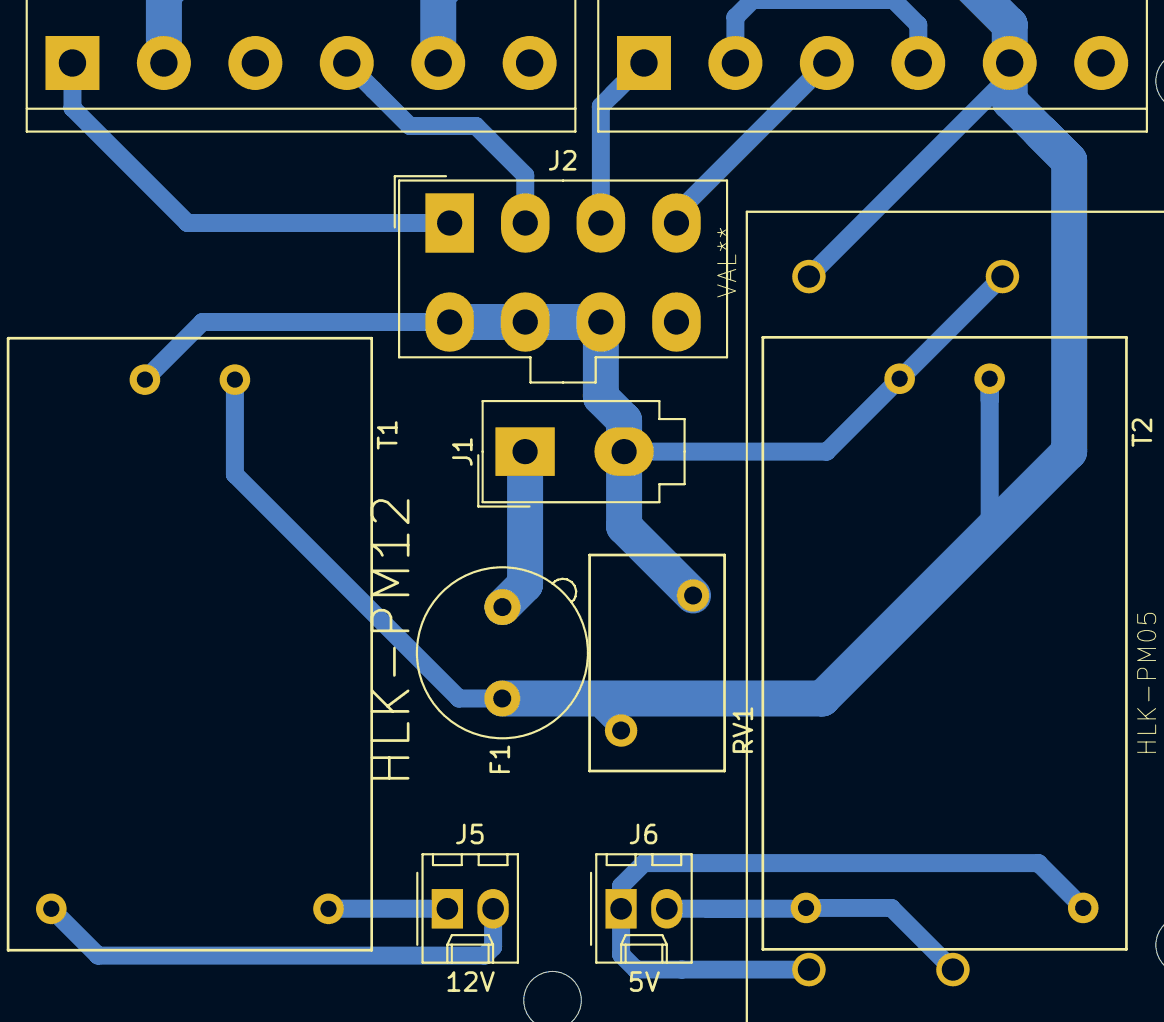
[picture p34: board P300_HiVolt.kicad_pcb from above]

Board: 2 copper layers, 11 parts (0 on the bottom side), 11 nets.

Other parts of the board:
Meanwell IRM-05-5: VAL**; CONV_IRM-05-5

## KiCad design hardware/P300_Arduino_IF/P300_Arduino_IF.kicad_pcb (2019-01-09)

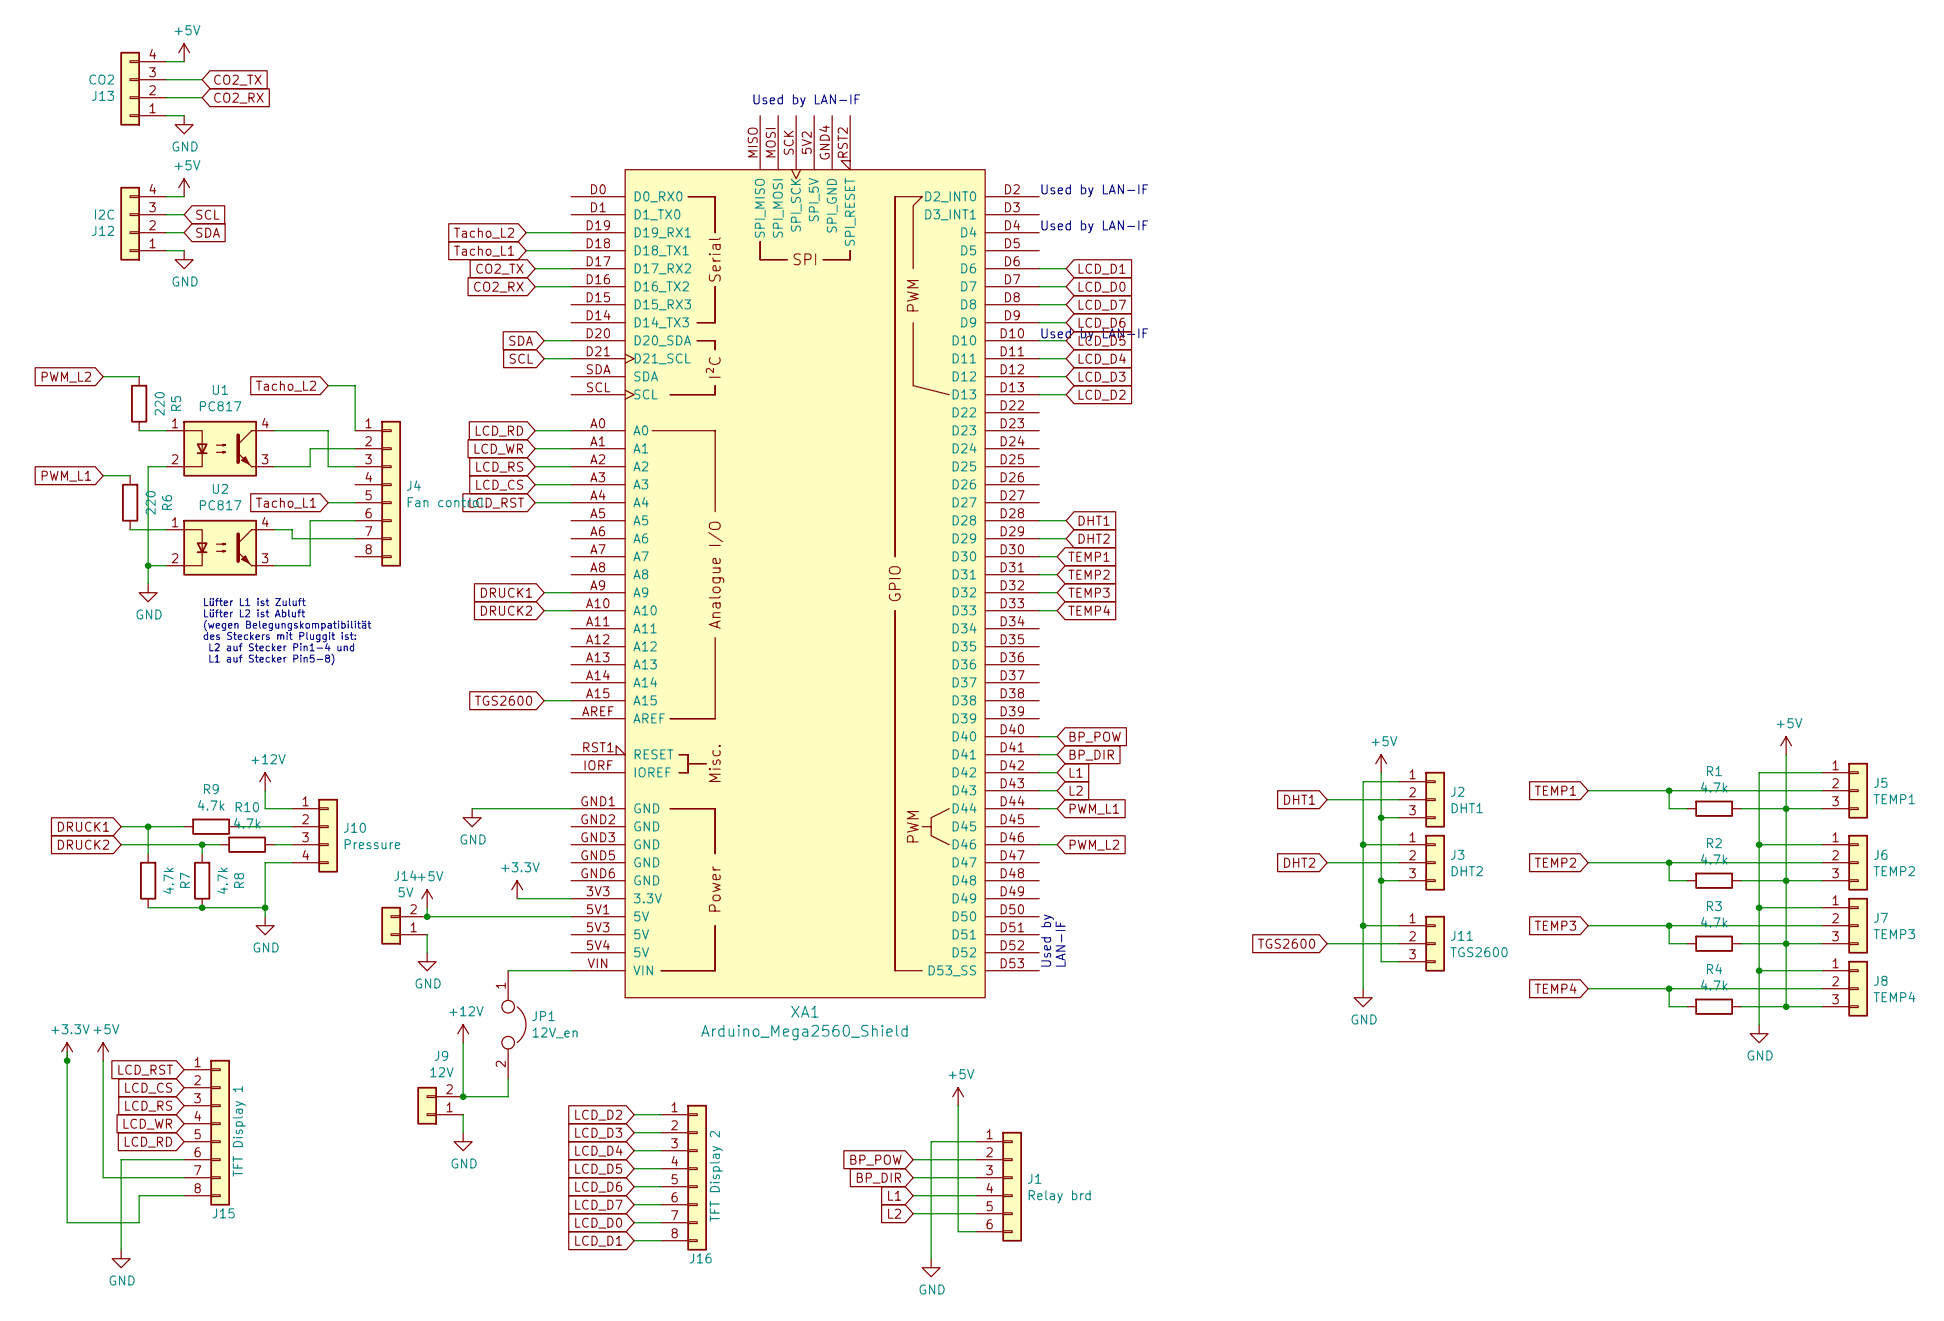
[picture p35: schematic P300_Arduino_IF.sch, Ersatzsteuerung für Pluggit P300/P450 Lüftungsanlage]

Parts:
J1: Relay brd; Molex_KK-254_AE-6410-06A_1x06_P2.54mm_Vertical
J2: DHT1; Molex_KK-254_AE-6410-03A_1x03_P2.54mm_Vertical
J3: DHT2; Molex_KK-254_AE-6410-03A_1x03_P2.54mm_Vertical
J4: Fan control; Molex_KK-254_AE-6410-08A_1x08_P2.54mm_Vertical
J5: TEMP1; Molex_KK-254_AE-6410-03A_1x03_P2.54mm_Vertical
J6: TEMP2; Molex_KK-254_AE-6410-03A_1x03_P2.54mm_Vertical
J7: TEMP3; Molex_KK-254_AE-6410-03A_1x03_P2.54mm_Vertical
J8: TEMP4; Molex_KK-254_AE-6410-03A_1x03_P2.54mm_Vertical
J9: 12V; Molex_KK-254_AE-6410-02A_1x02_P2.54mm_Vertical
J10: Pressure; Molex_KK-254_AE-6410-04A_1x04_P2.54mm_Vertical
J11: TGS2600; Molex_KK-254_AE-6410-03A_1x03_P2.54mm_Vertical
J12: I2C; Molex_KK-254_AE-6410-04A_1x04_P2.54mm_Vertical
J13: CO2; Molex_KK-254_AE-6410-04A_1x04_P2.54mm_Vertical
J14: 5V; Molex_KK-254_AE-6410-02A_1x02_P2.54mm_Vertical
J15: TFT Display 1; Molex_KK-6410-08_08x2.54mm_Straight
J16: TFT Display 2; Molex_KK-254_AE-6410-08A_1x08_P2.54mm_Vertical
JP1: 12V_en; PinHeader_1x02_P2.54mm_Vertical
R1, R2, R3, R4: 4.7k; R_Axial_DIN0207_L6.3mm_D2.5mm_P10.16mm_Horizontal
R5, R6: 220; R_Axial_DIN0207_L6.3mm_D2.5mm_P2.54mm_Vertical
R7, R8, R9, R10: 4.7k; R_Axial_DIN0207_L6.3mm_D2.5mm_P2.54mm_Vertical
U1, U2: PC817; DIP-4_W7.62mm
XA1: Arduino_Mega2560_Shield; Arduino_Mega2560_Shield_no_ICSP

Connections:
+3V3: J15.8, XA1.3V3 (3.3V)
+5V: J1.6, J2.3, J3.3, J5.3, J6.3, J7.3, J8.3, J11.3, J12.4, J13.4, J14.2, J15.7, R1.1, R2.1, R3.1, R4.1, XA1.5V1 (5V)
+12V: J9.2, J10.1, JP1.2
BP_DIR: J1.3, XA1.D41
BP_POW: J1.2, XA1.D40
CO2_RX: J13.2, XA1.D16 (D16_TX2)
CO2_TX: J13.3, XA1.D17 (D17_RX2)
DHT1: J2.2, XA1.D28
DHT2: J3.2, XA1.D29
DRUCK1: R7.2, R9.2, XA1.A9
DRUCK2: R8.2, R10.2, XA1.A10
GND: J1.1, J2.1, J3.1, J4.4, J4.8, J5.1, J6.1, J7.1, J8.1, J9.1, J10.4, J11.1, J12.1, J13.1, J14.1, J15.6, R7.1, R8.1, U1.2, U2.2, XA1.GND1 (GND)
L1: J1.4, XA1.D42
L2: J1.5, XA1.D43
LCD_CS: J15.2, XA1.A3
LCD_D0: J16.7, XA1.D7
LCD_D1: J16.8, XA1.D6
LCD_D2: J16.1, XA1.D13
LCD_D3: J16.2, XA1.D12
LCD_D4: J16.3, XA1.D11
LCD_D5: J16.4, XA1.D10
LCD_D6: J16.5, XA1.D9
LCD_D7: J16.6, XA1.D8
LCD_RD: J15.5, XA1.A0
LCD_RS: J15.3, XA1.A2
LCD_RST: J15.1, XA1.A4
LCD_WR: J15.4, XA1.A1
unnamed: J4.2, U1.3
unnamed: J4.3, U1.4
unnamed: J4.6, U2.3
unnamed: J4.7, U2.4
unnamed: J10.2, R9.1
unnamed: J10.3, R10.1
unnamed: JP1.1, XA1.VIN
unnamed: R5.1, U1.1
unnamed: R6.1, U2.1
PWM_L1: R6.2, XA1.D44
PWM_L2: R5.2, XA1.D46
SCL: J12.3, XA1.D21 (D21_SCL)
SDA: J12.2, XA1.D20 (D20_SDA)
TEMP1: J5.2, R1.2, XA1.D30
TEMP2: J6.2, R2.2, XA1.D31
TEMP3: J7.2, R3.2, XA1.D32
TEMP4: J8.2, R4.2, XA1.D33
TGS2600: J11.2, XA1.A15
Tacho_L1: J4.5, XA1.D18 (D18_TX1)
Tacho_L2: J4.1, XA1.D19 (D19_RX1)

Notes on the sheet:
Used by LAN-IF
Used by LAN-IF
Lüfter L1 ist Zuluft Lüfter L2 ist Abluft (wegen Belegungskompatibilität des Steckers mit Pluggit ist: L2 auf Stecker Pin1-4 und L1 auf Stecker Pin5-8)

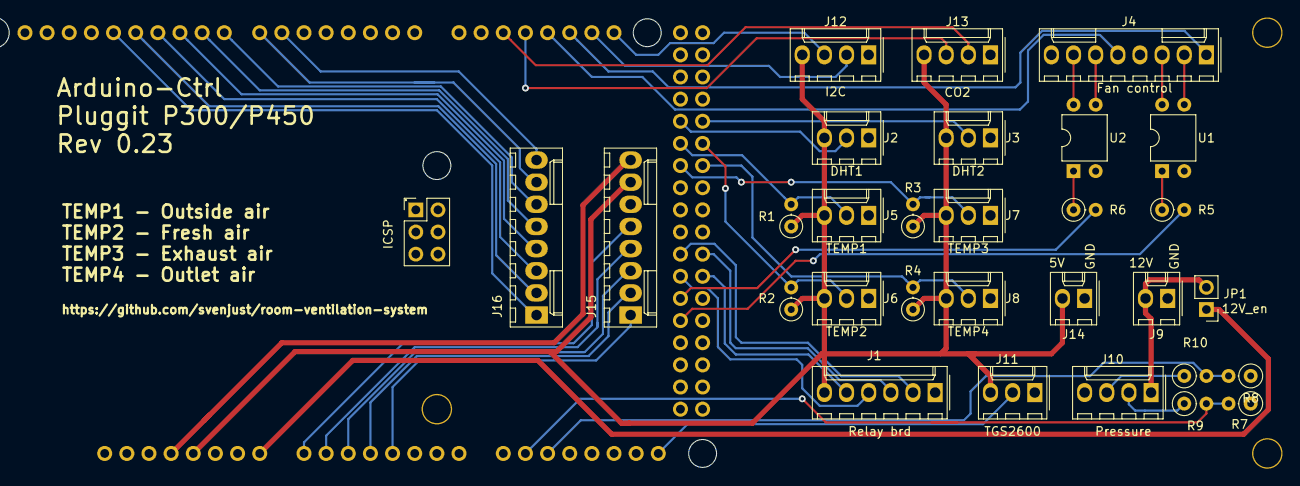
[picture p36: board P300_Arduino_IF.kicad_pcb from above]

Board: 2 copper layers, 31 parts (0 on the bottom side), 47 nets.

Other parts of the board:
ICSP: Pin_Header_Straight_2x03_Pitch2.54mm

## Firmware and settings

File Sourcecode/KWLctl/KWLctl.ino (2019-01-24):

/*
  ################################################################
  #
  #   Copyright notice
  #
  #   Control software for a Room Ventilation System
  #   https://github.com/svenjust/room-ventilation-system
  #
  #   Copyright (C) 2018  Sven Just (sven@familie-just.de)
  #
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
  #   This copyright notice MUST APPEAR in all copies of the script!
  #
  ################################################################
*/

/*
  # Steuerung einer Lüftungsanlage für Wohnhäuser

  Diese Steuerung wurde als Ersatz der Originalsteuerung entwickelt.

  Das Original war Pluggit P300. Diese Steuerung funktioniert ebenso für P450 und viele weitere Lüftungsanlagen.

  Es werden:
  1. zwei Lüfter angesteuert und deren Tachosignale ausgelesen
  2. vier Temperatursensoren abgefragt
  3. Steuerung Abluftventilator zum Frostschutz
  4. Optional: Vorheizregister als Frostschutz
  5. Optional: Sommer-Bypass geschaltet
  6. Optional: Vorheizregister als Frostschutz
  Die Drehzahlregelung der Lüftermotoren erfolgt durch PID-Regler. Dies sorgt dafür, das die geforderten Drehzahlen der Lüfter sicher erreicht werden. Die Leistungssteuerung des Vorheizregisters erfolgt durch einen PID-Regler.

  Differenzdrucksensoren werden bisher nicht berücksichtigt.

  Die Steuerung ist per LAN (W5100) erreichbar. Als Protokoll wird mqtt verwendet. Über mqtt liefert die Steuerung Temperaturen, Drehzahlen der Lüfter, Stellung der Bypassklappe und den Status der AntiFreeze Funktion zurück.
*/

#include "KWLControl.hpp"

#include <MultiPrint.h>

// Actual instance of the control system.
KWLControl kwlControl;

static void loopWrite100Millis() {
  auto currentMillis = millis();
  static unsigned long previous100Millis = 0;
  if (currentMillis - previous100Millis > 100) {
    previous100Millis = currentMillis;
    Serial.print (F("Timestamp: "));
    Serial.println(long(currentMillis));
  }
}

/**********************************************************************
  Setup Routinen
**********************************************************************/

// *** SETUP START ***
void setup()
{
  Serial.begin(57600); // Serielle Ausgabe starten

  // Timebase for PWM Signal
  //TCCR5B = (TCCR5B & 0xF8) | 0x02 ; // Timer 5, Divisor 8, Frequency 3.921 KHz
  TCCR5B = (TCCR5B & 0xF8) | 0x03 ; // Timer 5, Divisor 64, Frequency 490.1 Hz            // default
  //TCCR5B = (TCCR5B & 0xF8) | 0x05 ; // Timer 5, Divisor 1024, Frequency 30.63 Hz
  
  // *** TFT AUSGABE ***
  kwlControl.getTFT().setup();

  // Init tracer which prints to both TFT and Serial.
  static MultiPrint initTracer(Serial, kwlControl.getTFT().getTFTPrinter());

  initTracer.println(F("Booting... "));

  kwlControl.begin(initTracer);
}
// *** SETUP ENDE

// *** LOOP START ***
void loop()
{
  kwlControl.loop();
  //loopWrite100Millis();
}
// *** LOOP ENDE ***

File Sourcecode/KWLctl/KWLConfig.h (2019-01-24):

/*
 * Copyright (C) 2018 Sven Just (sven@familie-just.de)
 * Copyright (C) 2018 Ivan Schréter (schreter@gmx.net)
 *
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
 * This copyright notice MUST APPEAR in all copies of the software!
 */

/*!
 * @file
 * @brief Configuration of the project.
 *
 * @note DO NOT MODIFY THIS FILE. Put your configuration into UserConfig.h.
 *
 * If no UserConfig.h is provided, then defaults are used. If it is provided,
 * then defaults may be overridden there, by using lines in the form:
 *
 * CONFIGURE(name, value)
 * CONFIGURE(name, values...)
 *
 * for each configuration parameter from KWLConfig.
 *
 * File UserConfig.h is not tracked, so it's easy to define specific site
 * configuration without modifying the tracked source code. Most likely, you
 * will at least want to override network settings.
 *
 * @par Example:
 * @code
 * CONFIGURE(RelayOFF, OPEN)
 * CONFIGURE(NetworkIPAddress, 192, 168, 42, 201)
 * CONFIGURE(NetworkMACAddress, 0xAA, 0xBB, 0xCC, 0xDD, 0xEE, 0xFF)
 * CONFIGURE(PrefixMQTT, "ap300")
 * @endcode
 *
 * You can also define DEBUG macro in UserConfig.h to enable debugging MQTT messages.
 */
#define DEBUG

#pragma once

#include "ProgramData.h"

#include <FlashStringLiteral.h>
#include <PersistentConfiguration.h>
#include <Arduino.h>

class IPAddress;
class HardwareSerial;

/// Helper to construct IP address as a literal.
class IPAddressLiteral
{
public:
  constexpr IPAddressLiteral() = default;
  constexpr IPAddressLiteral(byte a, byte b, byte c, byte d) noexcept : ip{a, b, c, d} {}
  operator IPAddress() const noexcept;
  constexpr IPAddressLiteral operator&(const IPAddressLiteral& other) const noexcept {
    return IPAddressLiteral(ip[0] & other.ip[0], ip[1] & other.ip[1], ip[2] & other.ip[2], ip[3] & other.ip[3]);
  }
  constexpr IPAddressLiteral operator|(const IPAddressLiteral& other) const noexcept {
    return IPAddressLiteral(ip[0] | other.ip[0], ip[1] | other.ip[1], ip[2] | other.ip[2], ip[3] | other.ip[3]);
  }
  IPAddressLiteral(const IPAddress& a) noexcept;
  constexpr byte operator[](unsigned index) const noexcept {
    return ip[index];
  }
  byte& operator[](unsigned index) noexcept {
    return ip[index];
  }
private:
  byte ip[4] = {0};
};

/// Helper to construct MAC address as a literal.
class MACAddressLiteral
{
public:
  constexpr MACAddressLiteral() = default;
  constexpr MACAddressLiteral(byte a, byte b, byte c, byte d, byte e, byte f) : mac{a, b, c, d, e,f} {}
  void copy_to(byte* out) const { out[0] = mac[0]; out[1] = mac[1]; out[2] = mac[2]; out[3] = mac[3]; out[4] = mac[4]; out[5] = mac[5]; }
  constexpr byte operator[](unsigned index) const noexcept {
    return mac[index];
  }
  byte& operator[](unsigned index) noexcept {
    return mac[index];
  }
private:
  byte mac[6] = {0};
};

/// State of the bypass flap.
enum class SummerBypassFlapState : uint8_t
{
  UNKNOWN = 0,  ///< Unknown.
  CLOSED  = 1,  ///< Closed or closing.
  OPEN    = 2   ///< Open or opening.
};

/// Summer bypass operation mode.
enum class SummerBypassMode : uint8_t
{
  AUTO    = 0,  ///< Open/close automatically.
  USER    = 1   ///< Open/close on external command.
};

/// Maximum # of fan mode settings. Not configurable.
static constexpr unsigned MAX_FAN_MODE_CNT = 10;

/// Do not build debug mode. Define in UserConfig.h if desired.
#undef DEBUG

/// Default configuration, which can be overridden by the user configuration below.
template<typename FinalConfig>
class KWLDefaultConfig
{
protected:
  /// Helper for relay state.
  static constexpr int8_t OPEN = -1;
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

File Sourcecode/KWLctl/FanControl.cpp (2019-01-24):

/*
 * Copyright (C) 2018 Sven Just (sven@familie-just.de)
 * Copyright (C) 2018 Ivan Schréter (schreter@gmx.net)
 *
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
 * This copyright notice MUST APPEAR in all copies of the software!
 */

#include "FanControl.h"
#include "MQTTTopic.hpp"
#include "KWLConfig.h"

#include <StringView.h>

#include <Arduino.h>
#include <Wire.h>

/// Global instance used by interrupt routines.
static FanControl* instance_ = nullptr;

// MQTT timing:

/// Interval for scheduling fan regulation (1s)
static constexpr unsigned long FAN_INTERVAL = 1000000;
/// Interval for sending fan information (5s), if speed changed.
static constexpr unsigned long FAN_MQTT_INTERVAL = 5000000;
/// Interval for sending fan information unconditionally (2min).
static constexpr unsigned long FAN_MQTT_INTERVAL_OVERSAMPLING = 120000000;
/// Interval for sending mode information unconditionally (5min).
static constexpr unsigned long MODE_MQTT_INTERVAL = 300000000;
/// Only send fan speed if changed by at least 50rpm.
static constexpr int MIN_SPEED_DIFF = 50;

// Calibration timing:

/// Timeout for the entire calibration (10 minutes). If the calibration doesn't
/// succeed in time, it will be cancelled.
static constexpr unsigned long TIMEOUT_CALIBRATION = 600000000;
/// Timeout for the calibration of one PWM step (5 minutes).
static constexpr unsigned long TIMEOUT_PWM_CALIBRATION = 300000000;

// Define the aggressive and conservative Tuning Parameters
// Nenndrehzahl Lüfter 3200, Stellwert 0..1000 entspricht 0-10V
static constexpr double aggKp  = 0.25,  aggKi = 0.1, aggKd  = 0.001;
static constexpr double consKp = 0.05, consKi = 0.1, consKd = 0.001;


Fan::Fan(uint8_t id, uint8_t powerPin, uint8_t pwmPin, uint8_t tachoPin, float ipr) :
  rpm_(static_cast<FanRPM::multiplier_t>(FanRPM::RPM_MULTIPLIER_BASE / ipr)),
  power_(powerPin),
  pwm_pin_(pwmPin),
  tacho_pin_(tachoPin),
  fan_id_(id),
  pid_(&current_speed_, &tech_setpoint_, &speed_setpoint_, consKp, consKi, consKd, P_ON_M, DIRECT)
{}

void Fan::begin(void (*countUp)(), unsigned standardSpeed, float ipr)
{
  standard_speed_ = standardSpeed;
  rpm_.multiplier() = static_cast<FanRPM::multiplier_t>(FanRPM::RPM_MULTIPLIER_BASE / ipr);

  pid_.SetOutputLimits(0, 1000);
  pid_.SetMode(AUTOMATIC);
  pid_.SetSampleTime(1000); // TODO use constant slightly less than in fan interval?

  // Lüfter Speed
  pinMode(pwm_pin_, OUTPUT);
  digitalWrite(pwm_pin_, LOW);

  // Lüfter Tacho Interrupt
  pinMode(tacho_pin_, INPUT_PULLUP);
  auto intr = uint8_t(digitalPinToInterrupt(tacho_pin_));
  attachInterrupt(intr, countUp, KWLConfig::TachoSamplingMode);

  Serial.print(F("Fan pins(tacho/PWM), interrupt, std speed, ipr:\t"));
  Serial.print(tacho_pin_);
  Serial.print('\t');
  Serial.print(pwm_pin_);
  Serial.print('\t');
  Serial.print(intr);
  Serial.print('\t');
  Serial.print(standardSpeed);
  Serial.print('\t');
  Serial.println(ipr);

  // Turn on power
  power_.on();
}

void Fan::computeSpeed(int ventMode, FanCalculateSpeedMode calcMode)
{
  speed_setpoint_ = standard_speed_ * KWLConfig::StandardKwlModeFactor[ventMode];

  if (ventMode == 0) {
    tech_setpoint_ = 0 ;  // Lüfungsstufe 0 alles ausschalten
    return;
  }

  double gap = abs(speed_setpoint_ - current_speed_); //distance away from setpoint

  // Das PWM-Signal kann entweder per PID-Regler oder unten per Dreisatz berechnen werden.
  // TODO above comment seems invalid now
  if (calcMode == FanCalculateSpeedMode::PID) {
    if (gap < 1000) {
      pid_.SetTunings(consKp, consKi, consKd);
    } else {
      pid_.SetTunings(aggKp, aggKi, aggKd);
    }
    pid_.Compute();
  } else if (calcMode == FanCalculateSpeedMode::PROP) {
    tech_setpoint_ = pwm_setpoint_[ventMode];
  }

  // Grenzwertbehandlung: Max- / Min-Werte
  if (tech_setpoint_ < 0)
    tech_setpoint_ = 0;
  if (tech_setpoint_ > 1000)
    tech_setpoint_ = 1000;
}

void Fan::setSpeed(int id, uint8_t pwmPin, uint8_t dacChannel)
{
  if (KWLConfig::serialDebugFan) {
    Serial.print(F("Fan "));
    Serial.print(id);
    Serial.print(F(": \tgap: "));
    Serial.print(current_speed_ - speed_setpoint_);
    Serial.print(F("\tspeedTacho: "));
    Serial.print(current_speed_);
    Serial.print(F("\ttechSetpoint: "));
    Serial.print(tech_setpoint_);
    Serial.print(F("\tspeedSetpoint: "));
    Serial.println(speed_setpoint_);
    rpm_.dump(Serial);
  }

  // Setzen per PWM
  // Ausgabewert für Lüftersteuerung darf zwischen 0-10V liegen, dies entspricht 0..1023, vereinfacht 0..1000
  // 0..1000 muss umgerechnet werden auf 0..255 also durch 4 geteilt werden
  // max. Lüfterdrehzahl bei Papstlüfter 3200 U/min
  int tech = int(tech_setpoint_);
  analogWrite(pwmPin, tech / 4);

  // Setzen der Werte per DAC
  if (KWLConfig::ControlFansDAC) {
    byte HBy;
    byte LBy;

    HBy = byte(tech >> 8);   //HIGH-Byte berechnen
    LBy = byte(tech & 255);  //LOW-Byte berechnen
    Wire.beginTransmission(KWLConfig::DacI2COutAddr); // Start Übertragung zur ANALOG-OUT Karte
    Wire.write(dacChannel);                   // Fan channel schreiben
    Wire.write(LBy);                          // LOW-Byte schreiben
    Wire.write(HBy);                          // HIGH-Byte schreiben
    Wire.endTransmission();                   // Ende
  }
}

void Fan::debugSet(int ventMode, int techSetpoint) {
  if (techSetpoint < 0)
    techSetpoint = 0;
  else if (techSetpoint > 1000)
    techSetpoint = 1000;
  pwm_setpoint_[ventMode] = techSetpoint;
}

bool Fan::speedCalibrationStep(int mode)
{
  if (abs(KWLConfig::StandardKwlModeFactor[mode]) < 0.01) {
    // Faktor Null ist einfach
    calibration_pwm_setpoint_[mode] = 0;
    return true;
  } else {
    // Faktor ungleich 0
    speed_setpoint_ = standard_speed_ * KWLConfig::StandardKwlModeFactor[mode];

    int maxGap = (speed_setpoint_ / 100 * KWLConfig::StandardKwlFanPrecisionPercent) + 1 ;  // max. StandardKwlFanPrecisionPercent % Abweichung 
    double gap = abs(speed_setpoint_ - current_speed_); //distance away from setpoint
    if ((gap < maxGap) && (good_pwm_setpoint_count_ < REQUIRED_GOOD_PWM_COUNT)) {
      // einen PWM Wert gefunden
      good_pwm_setpoint_[good_pwm_setpoint_count_] = int(tech_setpoint_);
      good_pwm_setpoint_count_++;
    }
    if (good_pwm_setpoint_count_ >= REQUIRED_GOOD_PWM_COUNT) {
      // fertig, genug Werte gefunden, jetzt Durchschnitt bilden
      long sum_pwm = 0;
      for (unsigned i = 0; i < REQUIRED_GOOD_PWM_COUNT; i++) {
        sum_pwm += good_pwm_setpoint_[i];
      }
      calibration_pwm_setpoint_[mode] = int(sum_pwm / REQUIRED_GOOD_PWM_COUNT);
      return true;
    }

    // Noch nicht genug Werte, PID Regler muss nachregeln
    if (gap < 1000)
      pid_.SetTunings(consKp, consKi, consKd);
    else
      pid_.SetTunings(aggKp, aggKi, aggKd);
    pid_.Compute();

    // !Kein PreHeating und keine Sicherheitsabfrage Temperatur
    return false;
  }
}
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

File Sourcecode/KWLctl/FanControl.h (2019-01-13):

/*
 * Copyright (C) 2018 Sven Just (sven@familie-just.de)
 * Copyright (C) 2018 Ivan Schréter (schreter@gmx.net)
 *
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
 * This copyright notice MUST APPEAR in all copies of the software!
 */

/*!
 * @file
 * @brief Fan regulation and status reporting.
 */
#pragma once

#include "Relay.h"
#include "KWLConfig.h"

#include <FanRPM.h>
#include <TimeScheduler.h>
#include <MessageHandler.h>

#include <PID_v1.h>

class Print;
class KWLPersistentConfig;

class MessageHandler;

/// Fan operation modes.
enum class FanMode : uint8_t
{
  Normal = 0,       ///< Normal operation.
  Calibration = 1   ///< Calibration in progress.
};

/// Fan speed calculation mode.
enum class FanCalculateSpeedMode : int8_t
{
  PID = 1,          ///< Use PID regulator (calibration and continuous calibration).
  PROP = 0,         ///< Use simple proportional calculation to PWM signal (normal operation).
  UNSET = -1        ///< Not set.
};

/// One fan handler.
class Fan
{
public:
  /*!
   * @brief Construct one fan interface.
   *
   * @param id fan ID for display purposes (1 or 2).
   * @param powerPin pin on which to drive power relay.
   * @param pwmPin pin on which to send PWM signal.
   * @param tachoPin pin on which to read tacho pulses.
   * @param ipr tacho signal count per rotation.
   */
  Fan(uint8_t id, uint8_t powerPin, uint8_t pwmPin, uint8_t tachoPin, float ipr = 1.0);

  /*!
   * @brief Start the fan.
   *
   * @param countUp interrupt routine which calls interrupt() for this fan to count RPM.
   * @param standardSpeed standard speed to use initially (in RPM).
   * @param ipr tacho signal count per rotation.
   */
  void begin(void (*countUp)(), unsigned standardSpeed, float ipr = 1.0);

  /// Get current speed (RPM) of this fan.
  inline unsigned getSpeed() const { return unsigned(current_speed_); }

  /// Get speed (RPM) for the standard ventilation mode.
  inline unsigned getStandardSpeed() const { return standard_speed_; }

  /// Set speed (RPM) for the standard ventilation mode.
  inline void setStandardSpeed(unsigned speed) { standard_speed_ = speed; }

  /// Check whether the fan is set off.
  inline bool isOff() const { return abs(tech_setpoint_) < 0.1; }

  /// Set the fan to off (until next computation).
  inline void off() { tech_setpoint_ = 0; }

  /// Get PWM signal strength for given ventilation mode.
  inline int getPWM(unsigned mode) const { return pwm_setpoint_[mode]; }

  /// Set PWM signal strength for given ventilation mode at initialization time.
  inline void initPWM(unsigned mode, int pwm) { pwm_setpoint_[mode] = pwm; }

  /// Set tacho signal impulses per rotation for this fan.
  void setImpulsesPerRotation(float ipr) {
    rpm_.multiplier() = static_cast<FanRPM::multiplier_t>(FanRPM::RPM_MULTIPLIER_BASE / ipr);
  }
private:
  friend class FanControl;

  /// Called by the interrupt routine for this fan.
  inline void interrupt() { rpm_.interrupt(); }

  /// Called by the fan control to update speed from RPM measurement.
  inline void updateSpeed() { current_speed_ = rpm_.getSpeed(); }

  /// Update fan speed based on modes.
  void computeSpeed(int ventMode, FanCalculateSpeedMode calcMode);

  /// Set computed fan speed via PWM pin and/or DAC.
  void setSpeed(int id, uint8_t pwmPin, uint8_t dacChannel);

  /// Debug: set PWM signal explicitly for debugging purposes.
  void debugSet(int ventMode, int techSetpoint);

  /// Prepare for calibration.
  void prepareCalibration() { good_pwm_setpoint_count_ = 0; }

  /// Perform one speed calibration step for given mode.
  bool speedCalibrationStep(int mode);

  /// Finish calibration and copy temp PWM values to real PWM values.
  void finishCalibration();

  /// Set debugging mode for this fan via MQTT.
  inline void debug(bool on) { mqtt_send_debug_ = on; }

  /// Send MQTT debugging message, if on.
  void sendMQTTDebug(int id, unsigned long ts, MessageHandler& h);

  /// How many "good" measurements do we need to consider the calibration good.
  static constexpr unsigned REQUIRED_GOOD_PWM_COUNT = 30;

  FanRPM rpm_;  ///< Speed measurement and setting.
  Relay power_; ///< Power relay.

  double current_speed_ = 0;            ///< Current speed of the fan in RPM.
  double speed_setpoint_ = 0;           ///< Desired speed of the fan in RPM.
  double tech_setpoint_ = 0;            ///< Needed PWM signal to set this fan speed.
  unsigned standard_speed_ = 0;         ///< Standard speed of this fan (configuration for default ventilation mode).
  int pwm_setpoint_[MAX_FAN_MODE_CNT];  ///< Current set of PWM output for ventilation modes.
  int calibration_pwm_setpoint_[MAX_FAN_MODE_CNT];  ///< Temporary PWM values during calibration.
  int good_pwm_setpoint_[REQUIRED_GOOD_PWM_COUNT];  ///< PWM signal strength considered "good" during calibration.
  unsigned good_pwm_setpoint_count_ = 0;            ///< # of "good" PWM signal strengths we already know.
  bool mqtt_send_debug_ = false;        ///< Send debugging info for this fan per MQTT.
  uint8_t pwm_pin_;                     ///< Pin to send PWM signa to.
  uint8_t tacho_pin_;                   ///< Pin to read tacho signal from.
  uint8_t fan_id_;                      ///< Fan ID (1 or 2).
  PID pid_;                             ///< PID regulator for this fan.
};
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

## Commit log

2017-12-11 mqtt-Debug Msg
    [mqtt_topics.ods]
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2017-12-12 Try: tachoPinFan; Zuweisung von Pin und Interrupt unterschieden. digitalPinToInterrupt liefert den Interrupt eines Pins
2017-12-12 Bugfix: Umrechnung von Pin zu Interrupt fehlte
    [KWLctl.ino]
2017-12-14 Reset/Werkszustand per mqtt topic d15/set/kwl/resetAll_IKNOWWHATIMDOING
    [KWLctl.ino]
2017-12-14 Bugfixing: Kalibrierung per mqtt startbar
    [KWLctl.ino]
2017-12-20 Bugfix und Serial.println für Sommer-Bypass
    [KWLctl.ino]
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2018-01-01 DHT11 hinzugefügt
    [mqtt_topics.ods]
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2018-01-16 update mqtt Topics
    [mqtt_topics.ods]
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2018-01-18 Debugging: Menü ohne Taste korrigiert
    [KWLctl.ino]
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2018-03-01 EffiencyKwl bei dem mqtt-Topics hinzugefügt. Der Wirkungsgrad wird zusammen mit den Temperaturen per mqtt übertragen
    [mqtt_topics.ods]
2018-03-01 Korrektur der Ausgabe von Temperaturen zwischen -0.9 und 0 Grad auf dem Display. Diese wurde ohne Vorzeichen als 0 bis 0.9 ausgegeben.
2018-03-01 Reihenfolge der Einzelloops verändert. Erst rechnen, dann per mqtt publishen, dann im Display anzeigen.
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2018-03-07 AntiFreeze - Forstschutzschaltung umgebaut und Kaminbetrieb ergänzt, Doku
    [mqtt_topics.ods]
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2018-07-09 Work on cleaning up the source code by explicitly specifying user configuration in a separate file.
    Example on IP address, standard settings and relay control.
    This method has the advantage of using less space for the configuration
    of complex objects (like IP address), since these are just compile-time
    literals instead of real variables. Thus, more RAM space is available
    for useful stuff.
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2018-07-09 Update circuit diagram: power suppy for Arduino is 5V pin not Vin
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2018-07-09 Create NetworkClient module
    This required two larger changes:
    - refactoring startup routines a bit, since initialization order w.r.t. libraries was not given
    - storing MQTT topics in Flash, since too little memory was left (obviously before it was just a few bytes short of crashing)
    [FanControl.cpp, FanControl.h, KWLConfig.h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]
2018-07-09 Add microscopic NTP client to get current time + weekday from NTP server
2018-07-09 Create small class to hold time in HH:MM:SS format and to print it out
2018-07-09 Rename start() to begin() to match naming convention in other Arduino components
2018-07-09 Small fixes and memory reduction
    [FanControl.cpp, KWLConfig.h, KWLctl.ino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]
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2018-07-11 Summer bypass refactoring
    Separate bypass component
    Fix the naming and configuration of temperature hysteresis for antifreeze (it was using bypass as name) + adjust persistent config appropriately
    Add missing MQTT topics to set bypass temperature limits
    [Antifreeze.cpp, Antifreeze.h, KWLConfig.h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]
2018-07-13 Send error and info bits via statusbits message, rework error loop
    [KWLConfig.h, KWLctl.ino]
2018-07-13 Wrap TFT and extra sensor handling into tasks to get runtime statistics
2018-07-14 Remove FL() function, as it is not working properly in all cases. Replace usages appropriately.
    [KWLctl.ino, NetworkClient.cpp]
2018-07-14 Print EEPROM contents only on serial console, not to TFT
    Also position cursor correctly on TFT during booting
    [KWLctl.ino]
2018-07-14 Significantly reduce number of files in sketch directory
    Move some stuff into libraries inside of the project. Makes building a tick more complex, since the libraries must be linked from Arduino libraries directory (script provided).
2018-07-15 Wrap additional sensor into own class, make it real cpp file
    Still TODO to clean it up - unnecessary millis queries, unsafe MQTT publish, etc.
2018-07-15 Make TFT handling and KWLControl real cpp files
    Now only a minimal skeleton remains in ino file to satisfy Arduino IDE requirements. Refactoring to use Task for TFT and additional sensors still open.
2018-07-15 Fix network initialization
    Additional debugging for IP addresses and on MQTT receive side
    [Antifreeze.cpp, FanControl.cpp, KWLControl.cpp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]
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2018-07-20 Move scheduler to a library
    Also clean up the APIs to make it more generic, so it can be submitted to Arduino libs (not yet so far, but code as such is close to it)
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2018-07-21 Rework program manager MQTT topics, add documentation
    Also small fixes in string handling and network client
    [KWLConfig.h, NetworkClient.cpp, ProgramManager.cpp]
2018-07-22 Add crash handler and the possibility to query crashes
    [KWLConfig.cpp, KWLConfig.h, KWLControl.cpp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]
2018-07-22 Shorten MQTT topics, prepare for handling different prefix (to allow for multiple devices in the same broker; e.g., for test purposes or real devices)
    [NetworkClient.cpp]
2018-07-24 Report crash via status bits; document crash debugging and status info
    [KWLConfig.cpp, KWLConfig.h, KWLControl.cpp]
2018-07-24 Fix configuration of strings, simplify user configuration in general
    [KWLConfig.h, TFT.cpp]
2018-07-24 Fix language in summer bypass init
    [SummerBypass.cpp]
2018-07-24 Fix program selection handling to match documentation
    [ProgramManager.cpp]
2018-08-15 Fix fan RPM reading when fan stopped
    [FanControl.cpp, FanControl.h]
2018-08-17 NTP: add error bit if no NTP server available and upgrade to NTPv4
    [KWLControl.cpp, TFT.cpp]
2018-08-31 Additional sensors: minor corrections for VOC state and serial debug
    [AdditionalSensors.cpp]
2018-09-10 TFT: Rework fan config screen
    [TFT.cpp]
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2018-09-25 TFT: Setup menu with icons, also icons for buttons
    Add screenshots from setup menu and add icons credits.
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2018-12-10 CO2 Sensor wurde nach Einschalten nicht erkannt, nur nach Reset. Das Schreiben und Lesen der seriellen Schnittstelle zum CO2 Sensor vorab, behebt den Fehler.
    [AdditionalSensors.cpp]
2018-12-23 Ergänzt Schaltplan und Platine, V0.22-dev
    [P300_Arduino_IF.kicad_pcb, P300_Arduino_IF.sch, P300_HiVolt.kicad_pcb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]
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2019-01-05 Update der Platinen auf 0.23-dev
    Änderungen von 0.22 zu 0.23 - P300_Arduino_IF
    - Linke Seite der Platine vergrößert auf ArduinoMega-Größe
    - Stecker für Displayanschluß ergänzt
    - Fünf weitere Bohrungen für Befestigung ergänzt
    - Leiterbahnen im größeren Abstand zu Durchbohrungen und Bauteilen verlegt
    - Connector für J12 I2C nach links verschoben, damit ausreichend Platz für JTS Stecker
    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
    [P300_Arduino_IF-B.Cu.gbl, P300_Arduino_IF-B.Mask.gbs, P300_Arduino_IF-B.SilkS.gbo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]
2019-01-06 P300_Display_IF: Bohrlöcher für Befestigung hinzugefügt
    [P300_Display_IF-B.Cu.gbl, P300_Display_IF-B.Mask.gbs, P300_Display_IF-B.SilkS.gbo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]
2019-01-07 Masseverbindungen auf J4 ergänzt.
    Auf dem Stecker J4 (Lüfteranschluss) die vergessenen Masseverbindungen Pin 4 und Pin 8 ergänzt.
    [P300_Arduino_IF-B.Cu.gbl, P300_Arduino_IF-B.Mask.gbs, P300_Arduino_IF-B.SilkS.gbo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]
2019-01-09 Platinen V.23 in die Herstellung gegeben
    [P300_Arduino_IF-B.Cu.gbl, P300_Arduino_IF-B.Mask.gbs, P300_Arduino_IF-B.SilkS.gbo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]
2019-01-09 Footprint Arduino reduziert
    Für die Displayplatine wird nur eine Teil des Arduino Mega Footprint benötigt.
    [P300_Display_IF-B.Cu.gbl, P300_Display_IF-B.Mask.gbs, P300_Display_IF-B.SilkS.gbo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]
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2019-01-12 TFT: Display small status on the screensaver screen
    It shows just fan speed at random location on the screensaver screen.
    In case of error, the icon changes to red stop icon, when info is
    available, to yellow triangle icon.
    [TFT.cpp]
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2019-01-14 Update P300_HiVolt Platine
    - Anschluss zu Relais per Schraubklemmen, anstatt Molex Stecker, wegen der schwierigen Beschaffung und Crimpen der Molex Verbindung
    - Alternative für 5V Spannung Meanwell IRM-05-5 mit 5W(1A) Leistung hinzugefügt, empfohlen bei Verwendung Display
    - Platine 3mm verlängert
    - Bohr in Mitte/unten hinzugefügt
    - Leiterbahnen zu den Lüftern auf 2mm verbreitert
    [P300_HiVolt-B.Cu.gbl, P300_HiVolt-B.Mask.gbs, P300_HiVolt-B.SilkS.gbo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]
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2019-02-17 Platinen Update
    Änderungen von HW-0.25 zu HW-0.26 - P300_Arduino_IF
    - Korrektur externer Displayanschluss zum Arduino
    Änderungen von HW-0.23 zu HW-0.26 - P300_Display_IF
    - Korrektur Displayanschluss zum Display
    Änderungen von HW-0.23 zu HW-0.25 - P300_Arduino_IF
    - Ergänzung von externen Pullup-Widerstand und Glättungskondensator am Tachosignal
    [P300_Arduino_IF-B.Cu.gbl, P300_Arduino_IF-B.Mask.gbs, P300_Arduino_IF-B.Paste.gbp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]

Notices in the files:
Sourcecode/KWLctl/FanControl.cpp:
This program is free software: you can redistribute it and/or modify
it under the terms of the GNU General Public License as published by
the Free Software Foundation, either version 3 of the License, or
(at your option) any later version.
